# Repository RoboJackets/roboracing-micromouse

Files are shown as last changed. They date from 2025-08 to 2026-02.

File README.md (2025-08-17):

# 🚧 Welcome to RoboRacing Micromouse 🚧
## What is Micromouse?
Micromouse is a new member program designed with the intention of providing an introduction to the electrical and firmware side of developing robots as a part of RoboRacing, while also preparing for a fun and competitive racing competition! Members will work on their own "mouse" that will be able to solve a 16x16 maze as quickly as possible.

> Watch a detailed overview of the competition by the Veritasium YouTube Channel

Watch the Video! (https://www.youtube.com/watch?v=ZMQbHMgK2rw)

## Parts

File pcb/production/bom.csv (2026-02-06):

Designator | Footprint | Quantity | Value | LCSC Part #
_2 | ROBOBUZZ_0.8X | 1
 | ROBOJACKETS | 1
7.4_LIPO1 | JST_PH_B2B-PH-K_1x02_P2.00mm_Vertical | 1 | Battery
C1 | 1206 | 1 | C 0.22uF
C2 | 1206 | 1 | C 0.1uF
C3 | 1206 | 1 | C
D1, D2, D3, D4 | DIO_SFH_4545_copy | 4 | SFH_4545
D5, D6 | 1206 | 2 | LED
J1, J3, J4 | PinSocket_1x08_P2.54mm_Vertical | 3 | Conn_01x08
J1_MOTORENCODER1, J2_MOTORENCODER1 | PinSocket_1x06_P2.54mm_Vertical | 2 | Conn_01x06
Q1, Q3, Q5, Q7 | TO-92_Inline | 4 | BS170
Q2, Q4, Q6, Q8 | XDCR_TEFT4300 | 4 | TEFT4300
Q9 | TO-220-3_Vertical | 1 | FQP27P06
R1, R10, R11, R12, R13, R14, R15, R16, R17, R18, R1_2, R5, R6, R7, R8, R9 | 1206 | 16 | R_US
R19, R20 | 1206 | 2 | 4.7k
R2 | 1206 | 1 | 100/75
R21 | 1206 | 1 | 1k
R3 | 1206 | 1 | 1.3k
R4 | 1206 | 1 | 2k
SW2 | SW_Slide_SPDT_Angled_CK_OS102011MA1Q | 1 | SW_SPDT
TP1, TP2, TP3, TP4, TP5, TP6 | TestPoint_THTPad_D2.0mm_Drill1.0mm | 6 | TestPoint
U1 | Teensy4.1_LessHoles | 1 | Teensy_4.1
U2 | TO-220-3_Vertical | 1 | L7805

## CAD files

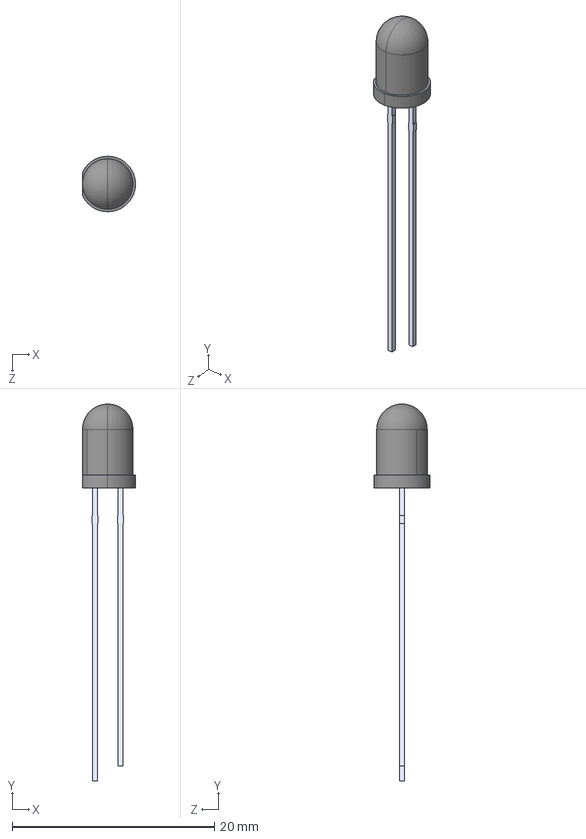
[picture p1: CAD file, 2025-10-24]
pcb/SFH_4545/SFH_4545.step
5.25 x 37.3 x 5.50 mm

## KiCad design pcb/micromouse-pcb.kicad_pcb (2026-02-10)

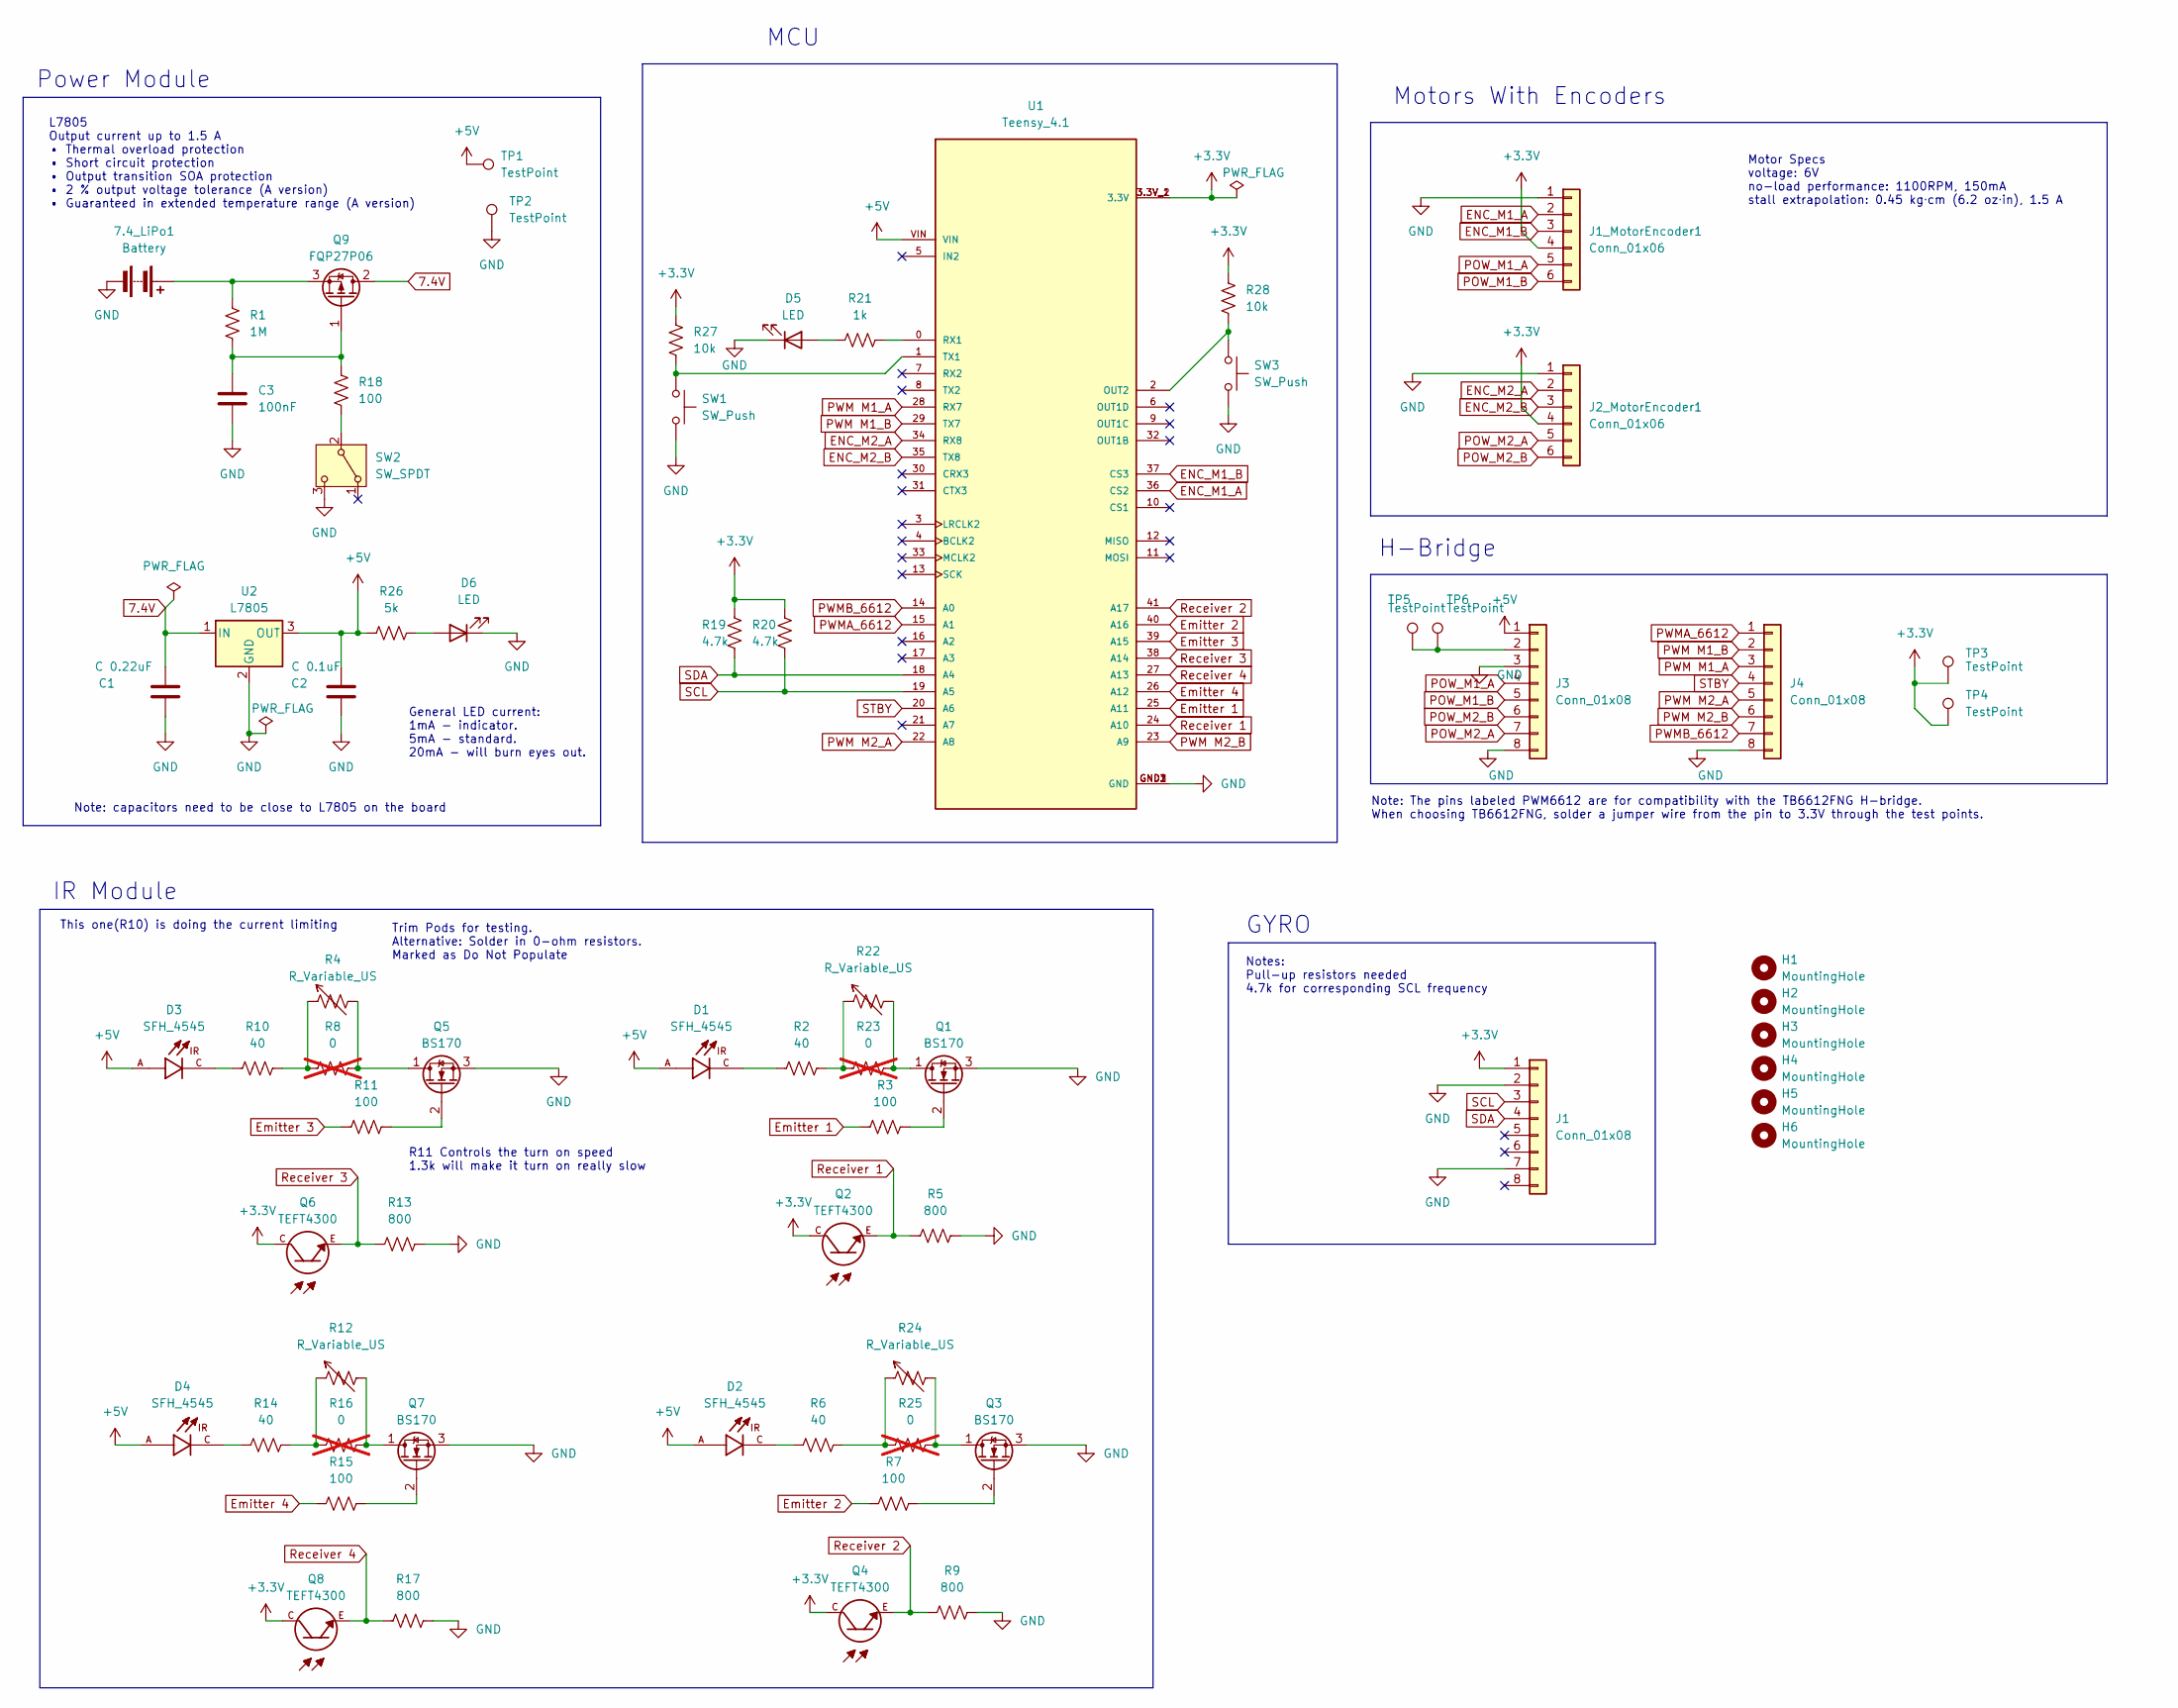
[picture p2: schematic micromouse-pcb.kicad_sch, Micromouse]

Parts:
7.4_LiPo1: Battery; JST_PH_B2B-PH-K_1x02_P2.00mm_Vertical
C1: C 0.22uF; C_1206_3216Metric_Pad1.33x1.80mm_HandSolder
C2: C 0.1uF; C_1206_3216Metric_Pad1.33x1.80mm_HandSolder
C3: 100nF; C_1206_3216Metric_Pad1.33x1.80mm_HandSolder
D1, D2, D3, D4: SFH_4545; DIO_SFH_4545_copy; PARTREV 1.5
D5, D6: LED; LED_1206_3216Metric_Pad1.42x1.75mm_HandSolder
H1, H2, H3, H4, H5, H6: MountingHole; MountingHole_4.3mm_M4
J1, J3, J4: Conn_01x08; PinSocket_1x08_P2.54mm_Vertical
J1_MotorEncoder1, J2_MotorEncoder1: Conn_01x06; PinSocket_1x06_P2.54mm_Vertical
Q1, Q3, Q5, Q7: BS170; TO-92_Inline
Q2, Q4, Q6, Q8: TEFT4300; XDCR_TEFT4300
Q9: FQP27P06; TO-220-3_Vertical
R1: 1M; R_1206_3216Metric_Pad1.30x1.75mm_HandSolder
R2, R6, R10, R14: 40; R_1206_3216Metric_Pad1.30x1.75mm_HandSolder
R3, R7, R11, R15, R18: 100; R_1206_3216Metric_Pad1.30x1.75mm_HandSolder
R4, R12, R22, R24: R_Variable_US; TRIM_PV36W203C01B00
R5, R9, R13, R17: 800; R_1206_3216Metric_Pad1.30x1.75mm_HandSolder
R8, R16, R23, R25: 0; R_1206_3216Metric_Pad1.30x1.75mm_HandSolder; not fitted
R19, R20: 4.7k; R_1206_3216Metric_Pad1.30x1.75mm_HandSolder
R21: 1k; R_1206_3216Metric_Pad1.30x1.75mm_HandSolder
R26: 5k; R_1206_3216Metric_Pad1.30x1.75mm_HandSolder
R27, R28: 10k; R_1206_3216Metric_Pad1.30x1.75mm_HandSolder
SW1, SW3: SW_Push; SW_SPST_B3SL-1002P
SW2: SW_SPDT; SW_Slide_SPDT_Angled_CK_OS102011MA1Q
TP1, TP2, TP3, TP4, TP5, TP6: TestPoint; TestPoint_THTPad_D2.0mm_Drill1.0mm
U1: Teensy_4.1; Teensy4.1_LessHoles; PARTREV 4.1
U2: L7805; TO-220-3_Vertical

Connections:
7.4V: C1.1, Q9.2 (D), U2.1 (IN)
+3.3V: J1.1, J1_MotorEncoder1.4, J2_MotorEncoder1.4, Q2.C, Q4.C, Q6.C, Q8.C, R19.1, R20.1, R27.1, R28.1, TP3.1, TP4.1, U1.3.3V_1 (3.3V), U1.3.3V_2 (3.3V)
+5V: C2.2, D1.A, D2.A, D3.A, D4.A, J3.1, R26.1, TP1.1, U1.VIN, U2.3 (OUT)
ENC_M1_A: J1_MotorEncoder1.2, U1.36 (CS2)
ENC_M1_B: J1_MotorEncoder1.3, U1.37 (CS3)
ENC_M2_A: J2_MotorEncoder1.2, U1.34 (RX8)
ENC_M2_B: J2_MotorEncoder1.3, U1.35 (TX8)
Emitter 1: R3.1, U1.25 (A11)
Emitter 2: R7.1, U1.40 (A16)
Emitter 3: R11.1, U1.39 (A15)
Emitter 4: R15.1, U1.26 (A12)
GND: 7.4_LiPo1.2 (-), C1.2, C2.1, C3.2, D5.1 (K), D6.1 (K), J1.2, J1.7, J1_MotorEncoder1.1, J2_MotorEncoder1.1, J3.3, J3.8, J4.8, Q1.3 (S), Q3.3 (S), Q5.3 (S), Q7.3 (S), R5.2, R9.2, R13.2, R17.2, SW1.2, SW2.3 (C), SW3.2, TP2.1, U1.GND1 (GND), U1.GND2 (GND), U1.GND3 (GND), U2.2 (GND)
unnamed: 7.4_LiPo1.1 (+), Q9.3 (S), R1.1
unnamed: D1.C, R2.1
unnamed: D2.C, R6.1
unnamed: D3.C, R10.1
unnamed: D4.C, R14.1
unnamed: D5.2 (A), R21.1
unnamed: D6.2 (A), R26.2
unnamed: J3.2, TP5.1, TP6.1
unnamed: Q1.1 (D), R22.2, R23.2
unnamed: Q1.2 (G), R3.2
unnamed: Q3.1 (D), R24.2, R25.2
unnamed: Q3.2 (G), R7.2
unnamed: Q5.1 (D), R4.2, R8.2
unnamed: Q5.2 (G), R11.2
unnamed: Q7.1 (D), R12.2, R16.2
unnamed: Q7.2 (G), R15.2
unnamed: C3.1, Q9.1 (G), R1.2, R18.1
unnamed: R2.2, R22.1, R23.1
unnamed: R4.1, R8.1, R10.2
unnamed: R12.1, R14.2, R16.1
unnamed: R6.2, R24.1, R25.1
unnamed: R18.2, SW2.2 (B)
unnamed: R28.2, SW3.1, U1.2 (OUT2)
unnamed: R21.2, U1.0 (RX1)
unnamed: R27.2, SW1.1, U1.1 (TX1)
POW_M1_A: J1_MotorEncoder1.5, J3.4
POW_M1_B: J1_MotorEncoder1.6, J3.5
POW_M2_A: J2_MotorEncoder1.5, J3.7
POW_M2_B: J2_MotorEncoder1.6, J3.6
PWM M1_A: J4.3, U1.28 (RX7)
PWM M1_B: J4.2, U1.29 (TX7)
PWM M2_A: J4.5, U1.22 (A8)
PWM M2_B: J4.6, U1.23 (A9)
PWMA_6612: J4.1, U1.15 (A1)
PWMB_6612: J4.7, U1.14 (A0)
Receiver 1: Q2.E, R5.1, U1.24 (A10)
Receiver 2: Q4.E, R9.1, U1.41 (A17)
Receiver 3: Q6.E, R13.1, U1.38 (A14)
Receiver 4: Q8.E, R17.1, U1.27 (A13)
SCL: J1.3, R20.2, U1.19 (A5)
SDA: J1.4, R19.2, U1.18 (A4)
STBY: J4.4, U1.20 (A6)

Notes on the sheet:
Trim Pods for testing. Alternative: Solder in 0-ohm resistors. Marked as Do Not Populate
Note: capacitors need to be close to L7805 on the board
General LED current: 1mA - indicator. 5mA - standard. 20mA - will burn eyes out.
GYRO
H-Bridge
This one(R10) is doing the current limiting
R11 Controls the turn on speed 1.3k will make it turn on really slow
Notes: Pull-up resistors needed 4.7k for corresponding SCL frequency
Power Module
IR Module
MCU
Motor Specs voltage: 6V no-load performance: 1100RPM, 150mA stall extrapolation: 0.45 kg⋅cm (6.2 oz⋅in), 1.5 A
Note: The pins labeled PWM6612 are for compatibility with the TB6612FNG H-bridge. When choosing TB6612FNG, solder a jumper wire from the pin to 3.3V through the test points.
Motors With Encoders
L7805 Output current up to 1.5 A • Thermal overload protection • Short circuit protection • Output transition SOA protection • 2 % output voltage tolerance (A version) • Guaranteed in extended temperature range (A version)

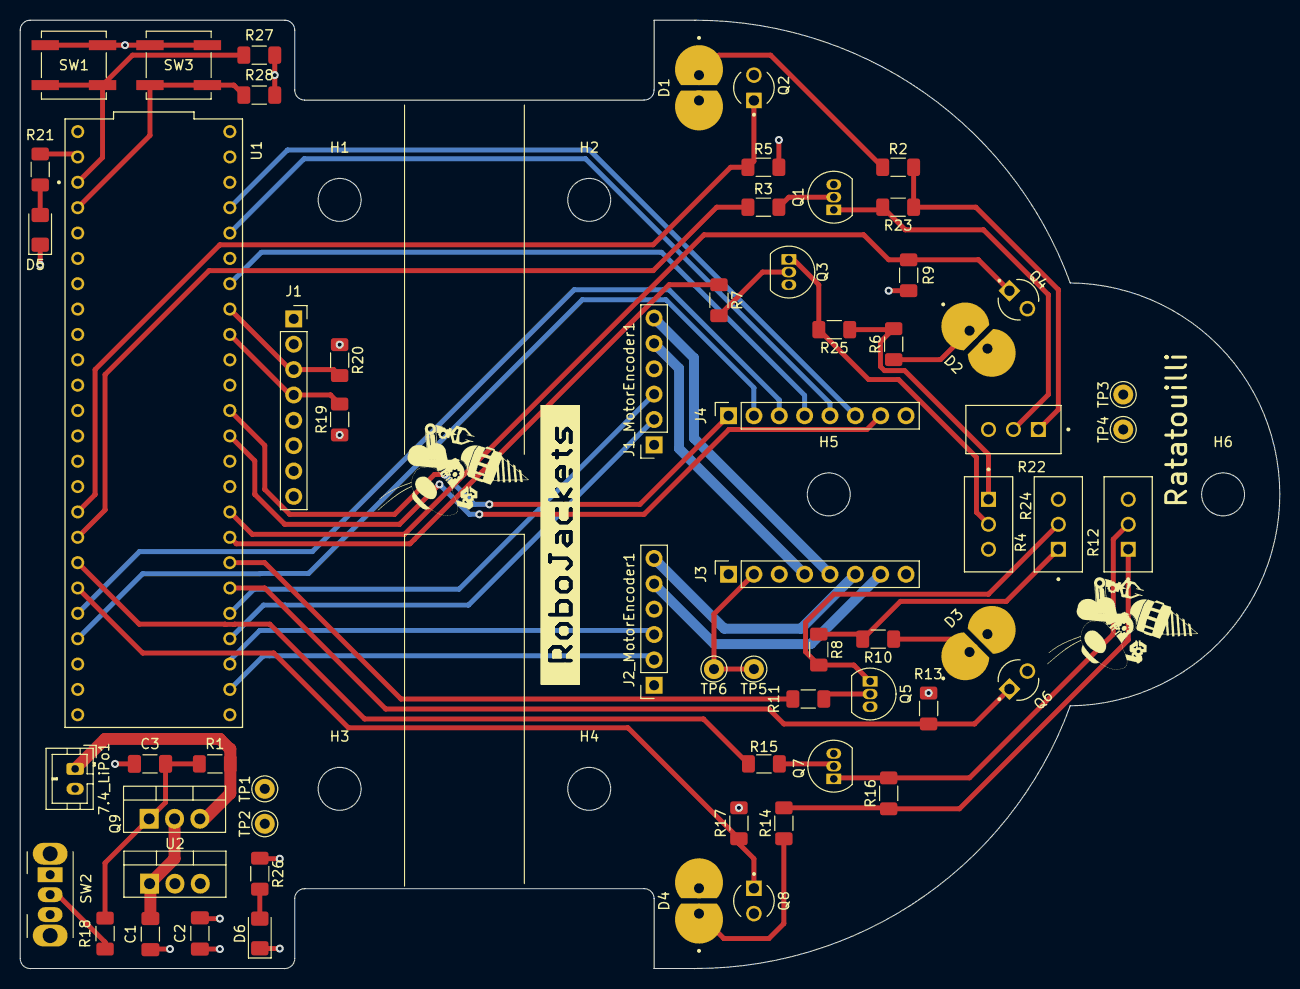
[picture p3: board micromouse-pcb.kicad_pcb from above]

Board: 4 copper layers, 126.2 x 95.0 mm, 69 parts (0 on the bottom side), 54 nets.

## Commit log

2025-10-12 uploaded crude beginnings of schematic and several footprints
    [MP1584EN-LF-Z.step, Micromouse1.kicad_pcb, Micromouse1.kicad_sch]
2025-10-24 added IR module and power module for PCB
    [Micromouse1.kicad_sch, SFH_4545.step, TEFT4300.step]
2025-10-26 Fixing bad symbol library management
    [MP1584EN-LF-Z.step, micromouse-pcb.kicad_pcb, micromouse-pcb.kicad_sch]
2025-10-26 added Kicad to .gitignore
2025-10-27 motor module connectors
    [micromouse-pcb.kicad_sch]
2025-10-27 changed connectors in motor module
    [micromouse-pcb.kicad_sch]
2025-10-27 schematic not updating?
    [micromouse-pcb.kicad_sch]
2025-10-31 worked a bit on motor module
    [micromouse-pcb.kicad_sch]
2025-11-02 finished motor module
    [micromouse-pcb.kicad_sch]
2025-11-02 !assigned random footprints, should be revised
    [micromouse-pcb.kicad_sch]
2025-11-03 basically done, changed a few footprints
    [micromouse-pcb.kicad_pcb, micromouse-pcb.kicad_sch]
2025-11-07 edited pcb
    [micromouse-pcb.kicad_pcb, micromouse-pcb.kicad_sch]
2025-11-14 worked on IR placement
    [micromouse-pcb.kicad_pcb]
2025-11-16 pcb design not connected yet; awaiting to be roasted in design review
    [micromouse-pcb.kicad_pcb]
2025-11-17 increased width to 8cm, placement done
    [micromouse-pcb.kicad_pcb]
2025-11-18 PCB FINISHED
    [micromouse-pcb.kicad_pcb]
2025-11-23 re-routed PCB with B.Cu as GND layer
2025-11-23 changed board outline for ball caster mount
    [micromouse-pcb.kicad_pcb, micromouse-pcb.kicad_sch]
2025-11-24 should be version after design review
    [micromouse-pcb.kicad_pcb, micromouse-pcb.kicad_sch]
2025-11-26 fixed footprint and silkscreens
    [micromouse-pcb.kicad_pcb]
2026-01-16 wider wires?
    [micromouse-pcb.kicad_pcb]
2026-01-16 Got gyro in
    [micromouse-pcb.kicad_pcb, micromouse-pcb.kicad_sch]
2026-01-16 made motor to H-bridge wires wider
    [micromouse-pcb.kicad_pcb]
2026-01-18 Slight changes to schematic
    [micromouse-pcb.kicad_pcb, micromouse-pcb.kicad_sch]
2026-01-18 Better file paths/directories
    [SFH_4545.step, TEFT4300.step, micromouse-pcb.kicad_pcb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]
2026-01-19 Reformatted schematic; Fixed Teensy & IR footprints; Changed Board Setups
    [micromouse-pcb.kicad_pcb, micromouse-pcb.kicad_sch]
2026-01-25 Done placement
    [SFH_4545.step, micromouse-pcb.kicad_pcb, micromouse-pcb.kicad_sch]
2026-01-25 Finished Routing!
    [micromouse-pcb.kicad_pcb, micromouse-pcb.kicad_sch]
2026-01-30 updated resistor values on schematic
    [micromouse-pcb-B_Cu.gbr, micromouse-pcb-B_Mask.gbr, micromouse-pcb-B_Paste.gbr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]
2026-02-06 Added trim pots and DNP resistors
    [bom.csv, designators.csv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]
2026-02-09 updated pcb with buttons
    [micromouse-pcb.kicad_pcb, micromouse-pcb.kicad_sch]
2026-02-09 Added robobuzz
    [micromouse-pcb.kicad_pcb]
2026-02-10 Added Ratatoulli name
    [micromouse-pcb.kicad_pcb, micromouse-pcb.kicad_sch]
